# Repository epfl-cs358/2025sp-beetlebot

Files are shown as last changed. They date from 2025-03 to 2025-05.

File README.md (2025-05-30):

<h1 align="center">CS-358 Project: BeetleBot 🪲</h1>

---

**Contributors:** Anna Barberis, Omayma Hadiji, Adèle Monjauze, Jonas Zimmermann, Anas El Madhi

BeetleBot Animation

## Project Description

BeetleBot is a six-legged robot with 3 degrees of freedom on each leg. The idea is to mimic the walking pattern of an insect, or more specifically to implement a tripod-like motion. Walking on flat ground, a hexapod can implement many different gaits to move itself. The most popular ones include tripod gait, going forward, backward, and rotating, an crab walk-like motion. 
Thus, a hexapod demonstrates flexibility in how it can move and balance its weight. Our robot moves itself based on an input given by a user through a web application. 
It interacts with its surrounding with three sensors posted on the front and the side. Read more on the [project proposal]().

## Table of Contents
- [Hardware & Design Specifications](#hardware-and-design-specifications)
- [Software Specifications](#software-specifications)
- [Challenges](#challenges)
- [Installation Requirements](#installation-requirements)
- [Make your own BeetleBot](#make-your-own-beetleBot)
- [Pinouts](#pinouts)
- [Usage Instructions](#usage-instructions)
- [Troubleshooting](#troubleshooting)
- [Acknowledgments](#acknowledgments)

## Hardware And Design Specifications

[View 3D Model](documentation/full_bot.stl)

The goal of our 3D design was to keep it lightweight, as compact as possible, and avoid any unnecessary plastic. This led to minimalistic legs with sturdy joints, using just enough material to hold the servos tightly, all while eliminating unwanted movement and making sure the servos weren’t supporting their own weight. The legs were also made in such a way that they could fold on themselves and go the most downwards possible. Indeed, the more the legs aligned under the body, the less force the servos would require to hold the whole hexapod. Standing up with your legs far apart is much harder than standing up with your legs close together. Being able to fold on themselves is a very important aspect that was needed when the hexapod was standing up: for example, if you come out of a swimming pool with your arms far from your body, you will have a hard time getting up, while if theyre are close to it, it will be much easier.

The base was designed to support the heaviest items on the bottom for better stability, while the lid holds the materials that require the most convenient access. This resulted in having 6 servos and the battery, along with its protection board and the buck converter, on the bottom as they hold the most weight. The ESP32 and the servo multiplexer were placed on top as we often needed to change the ESP's or the multiplexer's cabling. The 6 servos that served as coxas were placed downwards and on the base so they wouldnt require any unecessary additional structure by being directly screwed on the floor of the base.
Finally, the base was designed with many holes to lighten it.

The final weight of the hexapod is 495g with an approximate size of 11 * 8.5 * 8 cm³ without the legs and 11 * 35 * 15 cm³ with the legs spread apart for the width of 35 cm and with the legs at their lowest for the height of 15cm.

## Software Specifications
The robot is capable of rotational, directional movements as well as standing / sitting (pose transitions). The implementation of those gait patterns works alongside real-time feedback from 3 VL53L1X sensors. The robot is controlled remotely through a webserial, or through input on a terminal (serial monitor) when plugged-in. 
The webpage accepts directional commands (North, East...) with additional curve orientations (North east, North West). The user can choose to toggle, on the webpage, between translational or rotational movement, and can also choose to toggle on sensor detection. If the sensor detection is on, the cycle of movement will stop if an object is in front, or on the sides, at a given distance. 
Here is a video to show of the [sensors](images/IMG_0313.MOV).
Each of our gaits are pre-defined. Real-time interpolation of those pre-defined angles is computed so that each leg moves smoothly, ie a leg contains three servos, and synchronizes with the whole 18 servos. 

The webpage and all of its content is loaded on the flash memory with SPIFFS, which makes it last between resets and not sent when uploading code. The website is processed in main.cpp, which changes the IP address of the websocket defined in it. This websocket is used to send updates between the control panel and the ESP. This is how the ESP get the last input and how the web page get the sensors' distances (used to update animations). The website takes input with a keyboard or with the joystick shown on screen. Both methods send the exact same data to the ESP, to simplify how it is handled.
Here is a video to show off [everything](images/video_2025-05-30_16-48-52.mp4)
## Challenges

- Hardware:
    - The challenges for the CAD was mainly the leg: We initially had a first design where the leg was unecessary long and heavy, with an added effect of the servos having to handle their own weight along with the rest of the leg. We did not realise immediately the importance of the design, thinking the servos would be able to hold it in any case. In fact, even with our now optimised design, they still struggle carrying the whole weight. The leg being too long was also problematic because this made it impossible for the hexapod to stand up or walk without putting too much force on the servos. It took some time but we finally managed to create a minimalistric design where the servos were tightly screwed to their joint. In consequence, the legs were much lighter and the servos did not have to hold their own weight anymore.
    - Another hardware challenge was the cable management. Indeed, we were facing a trio of cables for each servos, along with cables for the multiplexer, the battery, the sensors and the ESP32, totalling with a strong ~50 cables. We managed to make some of them fit inside the base, but the biggest problems was the cables that had to stay outside of the base since the multiplexer was on the lid. We ended up tying the servo cables together so they would not be everywhere around our hexapod.  
- Software:
    - One of the main challenges was trying to implement inverse kinematics (IK). While the math behind it was well-understood on paper, translating it to code was a bit more compilcated. The IK computations relied heavily on real-world measurements, such as the exact lengths of the leg segments and the position of the servos, and small differences made the leg movement inaccurate or unexpected. Tuning those parameters was particularly difficult, and we were short on time to completely dive in and properly understand what was wrong and how to fix it. We made compromises by gradually introducing motion interpolation and hardcoding the gaits we wanted, as explained on the last section.
    - Another challenge we faced was implementing an interface to control the bot over WiFi. This has been done with multiple libraries that are listed in our platformio.ini. The most notable are the webserver and the websocket: The first just sends a file when a GET request arrive, while the second is set between the webapp and the ESP to exchange information during execution. The webapp sends the input the bot must follow, while the ESP sends the distances recorded by sensors. This task didn't create as much trouble for us as other ones, but it required a lot of background knowledge for the different APIs and how everything needed to be connected.

## Installation Requirements

- Hardware requirements (e.g., components needed).
    - Electronics:
        - 18 servos (in our case it was servo SG90 but we would heavily recommand stronger ones)
        - 3 sensors(TOF400C) to place in front and on the sides
        - PCA 9685 PWM multiplexer to plug the servos (would advise to have two multiplexers instead of just one)
        - Esp32 Devkit V1 Board as a micro controller, or any esp32 that has WiFi
        - LiPo Battery 25C 1000mAh 2S
        - Protection Board for the battery (2 cell BMS)
        - Jst connectors to connect the protection board and the battery
        - LM2596 Buck Converter
        - Cables and tape for the cable management (very important)
    - CAD components:
        - a base to hold the battery, 6 servos that will serve as the Coxas of the legs.
        - a lid to screw on top of the base, where we can place the multiplexer, the ESP32 and the buck converter.
        - 3 sensor holders to place in between the base and the lid
        - 6 legs composed of 3 pieces each:
            - a first joint to link the Coxa and the Femur
            - a second joint to link the Femur and the Tibia
            - a toe with a TCP tip
- Software requirements: Open the code folder inside VSCode, and install the PlatformIo Extension.
    - Platformio will automatically update itself with the library in platformio.ini, so the one we already wrote can be used directly.
    - To use the robot:
        - Go to the platformIO tab on VSCode, then go to your board > "Build Filesystem Image". After this is finished, use "Upload Filesystem Image". This will send the data folder, containing the website, to the ESP's flash memory.
        - Upload the code to the ESP.

## Make your own BeetleBot:
- Print all the 3D parts inside this [folder](CAD)
- Soldering :
    - solder the protection board : 2-jst female connector to the 8.4V for the (+) and 0V for the (-) : This will be where you plug your battery.
    - Solder the protection board 2 : thick cables on 12.6V for the (+) and 4.2V for the (-) : This will be for the consumer side.
    - Solder the thick cables to the buck converter
    - Solder some cables (preferably thick) from the out pins of the buck converter and connect it to the general (+) and (-) circuit of your system.
It should look like this :
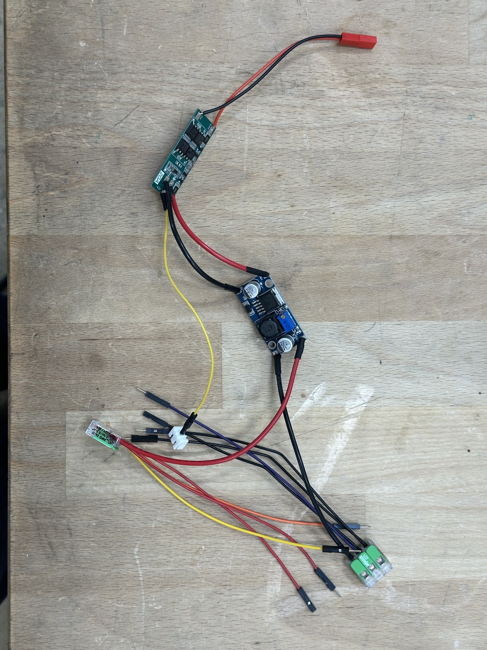
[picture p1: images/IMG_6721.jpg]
Soldering

- Screw on the 18 servos to the main body and on their joints: make sure to set them to a given angle (setAngle) inside data.h and put them on at a right angle to their joints
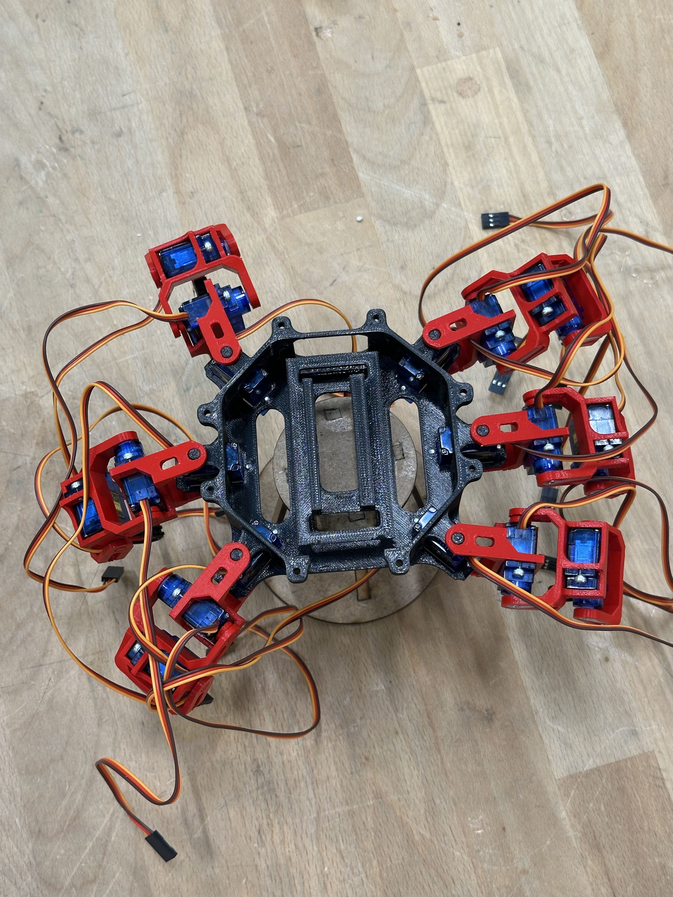
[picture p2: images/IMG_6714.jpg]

- Place the buck converter, the battery, the protection board, and the bundle of cables inside the body and screw on the lid on top
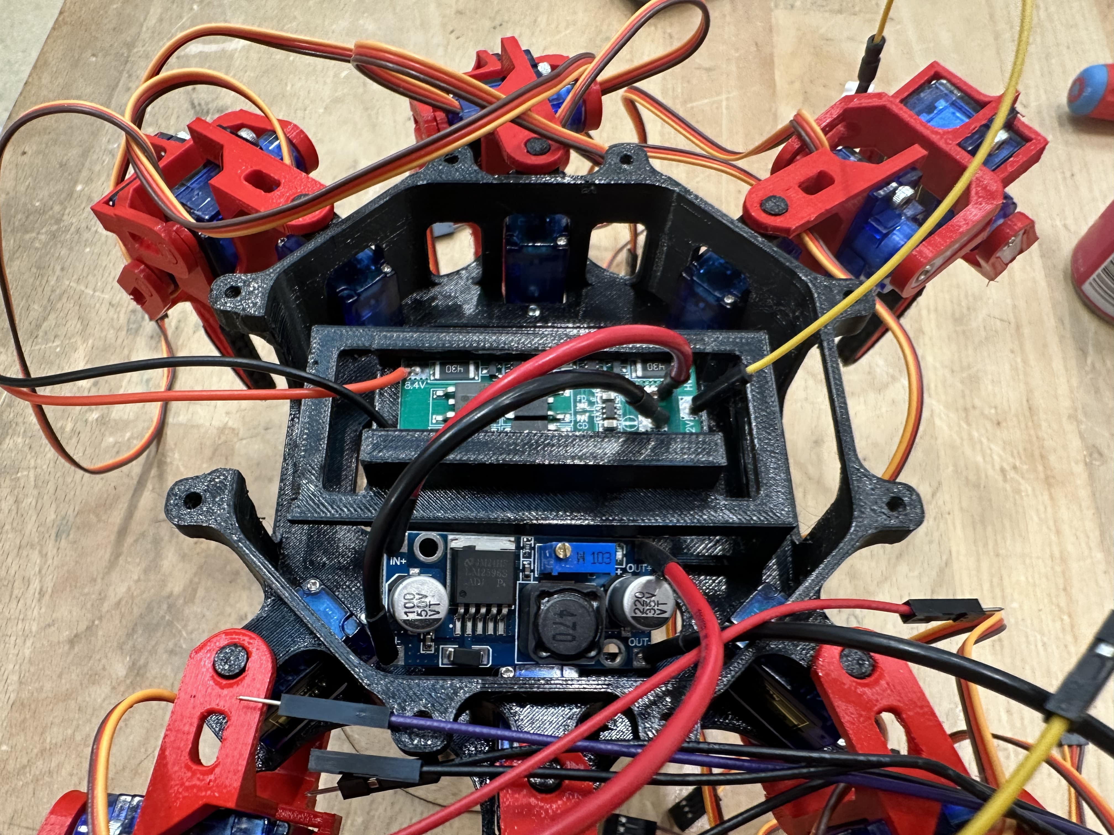
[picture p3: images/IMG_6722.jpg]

- Screw the multiplexer on the lid.
- Place the ESP32 in its sloth and crew the T stick figure on top to keep it in place.
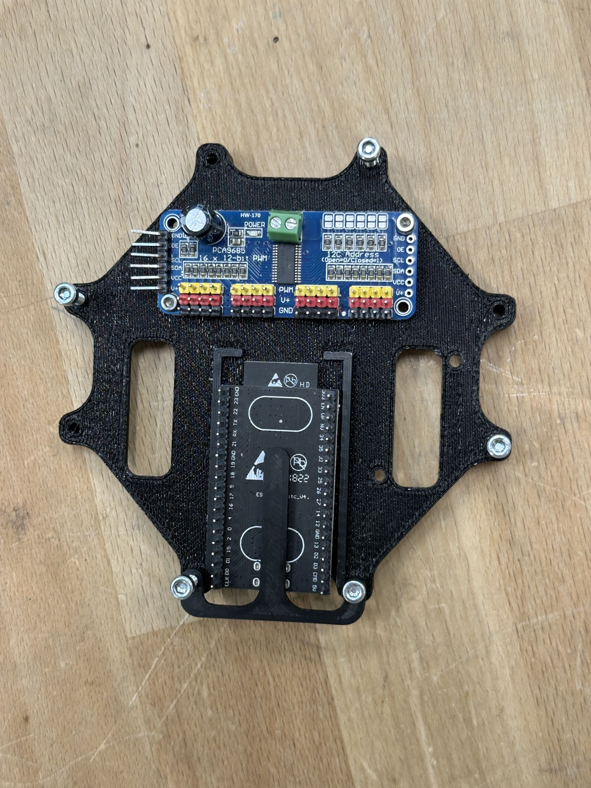
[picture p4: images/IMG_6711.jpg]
Lid

- Plug in all the servos on the multiplexer according to the mapping in the data.h, two of those servos (in our case the tibias of the two front legs) should be plugged in to the esp and powered from the power supply.
- Plug all the cables coming out of the multiplexer (SDA, SCL,...)
- Plug in the sensors on the esp, and screw them (or tape them).
- Finally, you can place a little hat on top and you're good to go!

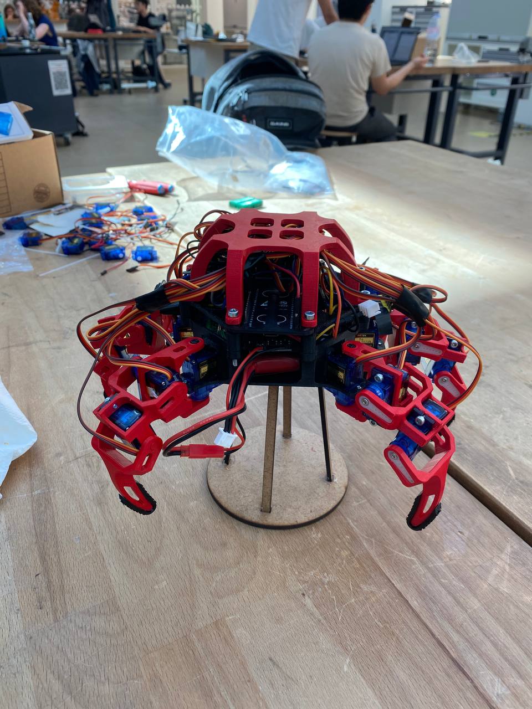
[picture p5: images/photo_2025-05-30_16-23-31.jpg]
Bot


## Pinouts
On Esp:
  - two servos PMW are plugged in on pin 18 and 23 of the ESP
  - SDA (pin 21) plugged to the multiplexer, and the sensors.
  - SCL (pin 22) plugged to the multiplexer, and the sensors.
  - 5V pin to power the esp
  - GND pin from the esp to the power supply

On the multiplexer:
  - Connect the power's (-) to the (-) of the multiplexer
  - Same for the (+)

For the sensors:
  - plug their SDA to the general SDA circuit
  - plug their SCL to the general SCL circuit
  - plug their (+) to the general (+) circuit
  - plug their (-) to the general (-) circuit

For the servos: plug them all on the multiplexer

Here is a picture of the circuit for additionnal help. Please note that for the cables that use the breadboard, this means you need to solder them together or clips them together :
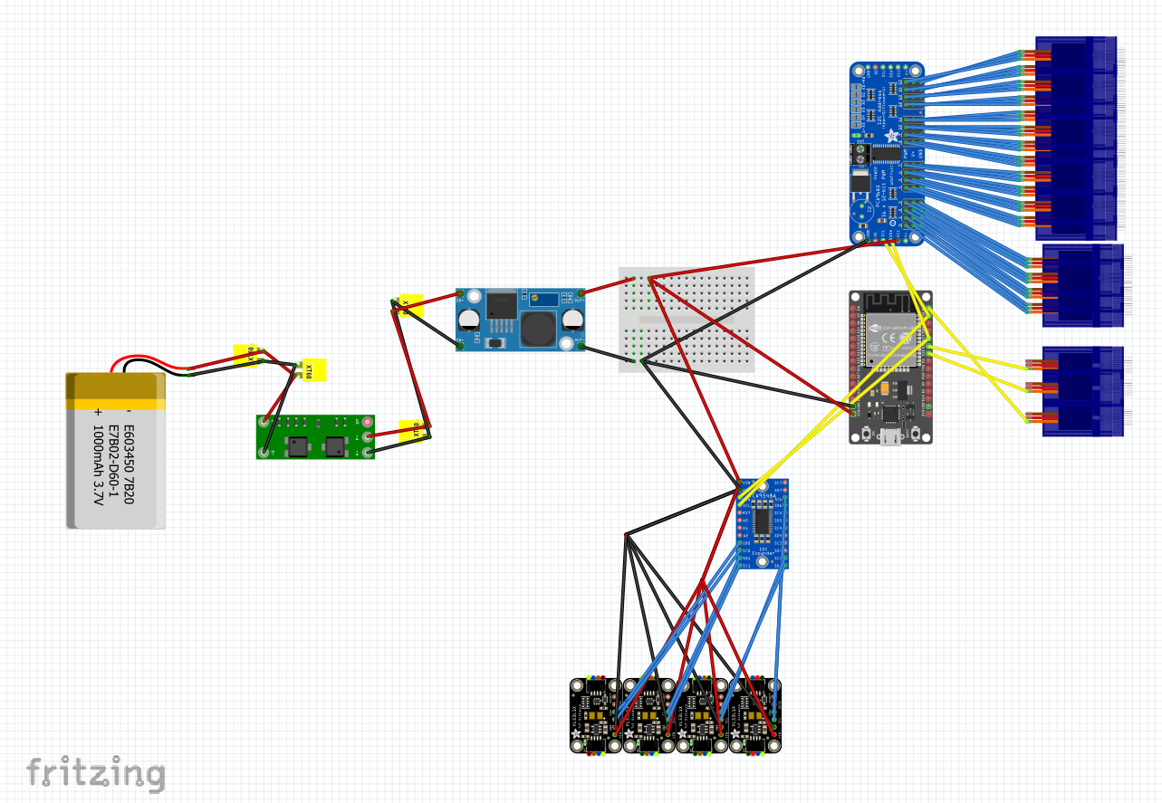
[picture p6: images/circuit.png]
Circuit Image

        
## Usage Instructions

Explain how to use your project. Include:
- Go on the wifi_credentials.h file
- Input the name of the wifi you will share with your ESP32 (You must both be on the same wifi)
- Put your wifi password
- Upload the code on the ESP32
- It will give you an IP adress: Copy paste it on your browser
- You will now be on the Web App: 
    - You can use the joystick to move around
    - You have different movement categories that you may change with the button 'change movement type'
    - Wether you are on AZERTY or QWERTZ, you can use THE WASD / ZQSD to move
- Have fun!
## Troubleshooting

There might be issues connecting to the ESP32 sometimes, it could be a port issue, if that is the case just look up and download 'CH340 driver'

## Acknowledgments

We'd like to thank all the servos and other components that had to die and/or suffer for this project to come to life! 

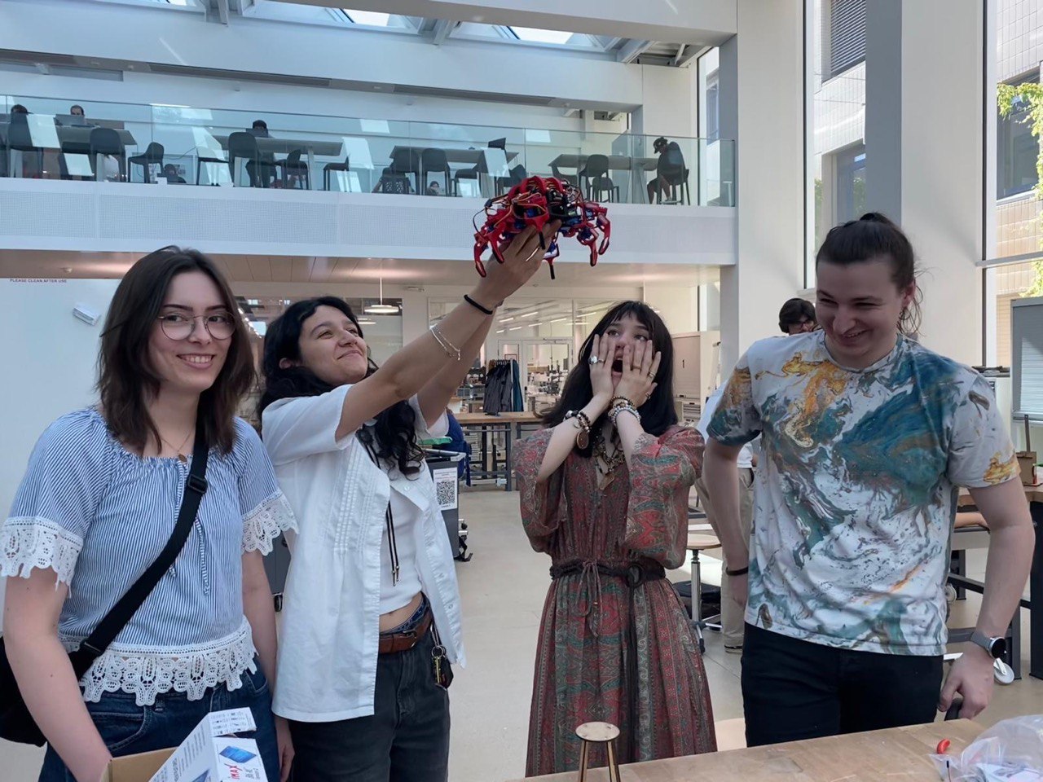
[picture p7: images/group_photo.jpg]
Group Photo


We thank all of our TAs and the teacher, especially Pinar Oray, Federico Stella and Mehdi Alaoui.

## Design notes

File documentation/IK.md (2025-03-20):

# Inverse Kinematics

## Introduction

Kinematics is the study of motion without considering the cause of such motion. such as forces and torques.
As opposed to forward kinematics, which computes the desired arrival coordinates of a robot given joint configuration as input, inverse kinematics (IK) is essentially the reverse operation, that is, computing joint configuration(s) to reach a desired arrival coordinate.
(**TLDR**: inverse kinematics is where you input where you want to go, and get the joint positions of how your robot needs to move in order to arrive at that position as output)

## Requirements

In order to compute the inverse kinematics of our BeetleBot, we will need the lengths of the joint sections, as well as some basic mechanical physics computations (into which we will input the joint lengths).

(The axis of the sketches are not indicative, they are only to visually show the different leg lengths)

<figure>
    <div style="display: flex; justify-content: space-between;">
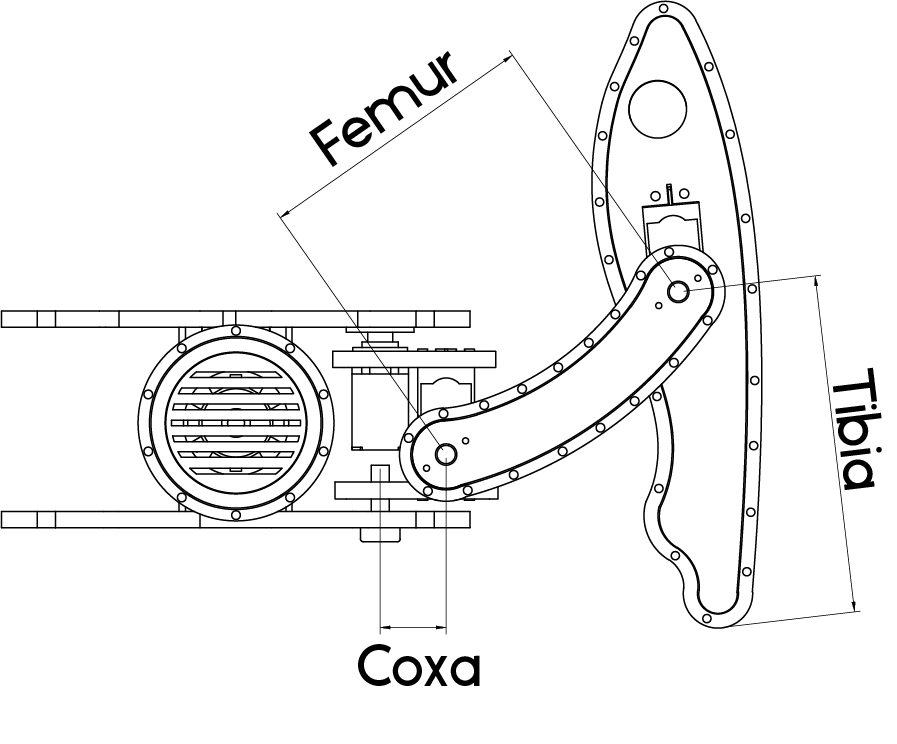
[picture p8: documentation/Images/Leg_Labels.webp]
Leg Labels
        
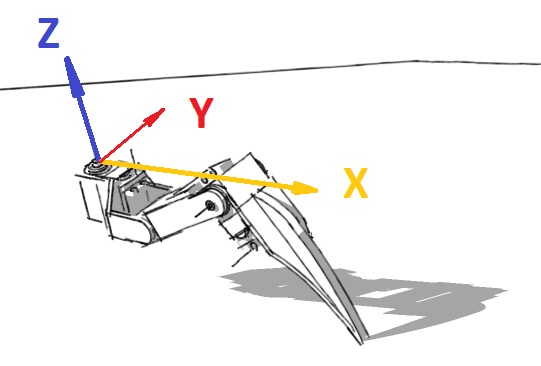
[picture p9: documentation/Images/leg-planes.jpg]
Leg Axis
        
    </div>
    <figcaption> Figure 1: Leg Labels (left) and Figure 2: Leg Axis (right) </figcaption>
</figure>

## Calculations

There are various online resources that have already done the brunt work of the mathematical and physics calculations that are needed in order to compute the inverse kinematics of walking robots. (I invite you to read up on the links in the sources for more precise details on the equations).
The [following](https://docs.google.com/spreadsheets/d/1CeIF2OFrUGDsMMskBs049kWXuV0JkgUp/edit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), (explanation [here](https://toglefritz.com/hexapod-inverse-kinematics-simulator/)) is a spreadsheet made to calculate all the required servo angles in order to have a basic translational walking gait. (Additional calculations will be needed in order to have different gaits, such as yaw, pitch, and roll, as illustrated via Figure 3.)

<figure>
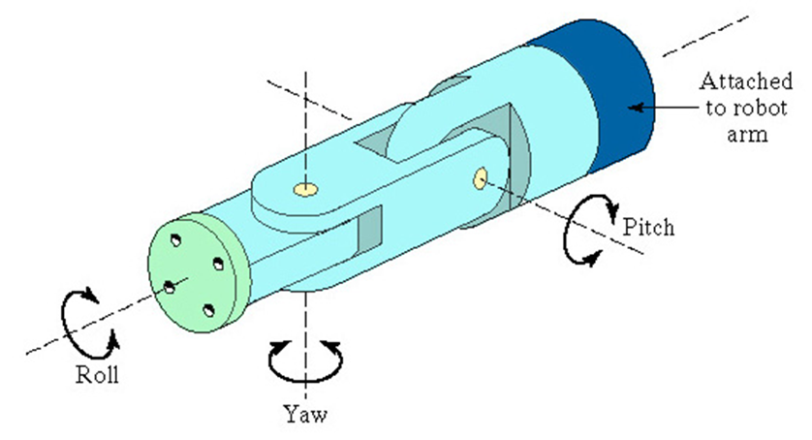
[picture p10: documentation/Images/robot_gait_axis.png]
Arm Axis
    
    <figcaption> Figure 3: Arm Gait Axis</figcaption>
</figure>

## Desired Movements

To achieve versatile and efficient movement, our hexapod robot should be capable of performing the following movements:
- Translational movement
  - Forward and Backward walking
  - Sideways walking (crab walk)
- Turning (Yaw)
- Pitch and Roll Adjustments

## Sources

- <https://toglefritz.com/hexapod-inverse-kinematics-equations/>
- <https://oscarliang.com/inverse-kinematics-and-trigonometry-basics/>
- <https://motion.cs.illinois.edu/RoboticSystems/InverseKinematics.html>

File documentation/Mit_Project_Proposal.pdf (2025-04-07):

# Proposal: BeetleBot

Anna Barberis, Omayma Hadiji, Jonas Zimmermann,

### Ad`ele Monjauze, Anas El Madhi

### March 2025

## 1 Description

The idea behind BeetleBot: BeetleBot, otherwise known as a Hexapod, is a six-legged robot with 3 degrees of freedom on each leg. The idea is to mimic the walking pattern of an insect, or more specifically to implement a tripod-like motion. Walking on flat ground, a hexapod can implement many different gaits to move itself. The most popular ones include tripod gait, reverse, and crab walk-like motion. The Beetlebot will also be able to interact and adapt to its surrounding, narrowing its stance to go through an obstacle-ridden path or avoiding objects ahead, to the sides, or behind itself. Thus, a hexapod demonstrates flexibility in how it can move and balance its weight. Our robot will respond to an input to direct itself, through a remote connection, like a game controller. It will also be able to make decisions based on its environment.

A deeper understanding: Stability is one of the keys to building a Hexapod. Using inverse kinematics equations, we will play with dynamic and static stability. Just like a human being can stand on one leg and shift his center of gravity, the same can be done for an hexapod (i.e. stand on half of its legs). If the center of mass of the robot is not probably balanced, the Hexapod will tip over.

### 1.1 Hardware

The selection of our electrical components was largely influenced by the choice of servos. To stay within our allocated budget while taking on the challenge of using relatively weak servos, we opted for SG90 servos to move the legs. They are lightweight, cheap, demand low power, and we have seen an existing project online that seemed to work using the full 18 of them. To connect the 18 + 1 servos together, we included a PCA 9685 PWM multiplexer. We also included 6 different servos, more powerful, but heavier and pricier. Those were included to be used on the weakest joint of the legs, the one that would bear the most weight, and that would be the most susceptible to break our SG90 servos. We plan to try with the weaker

1

servos first, and then decide later on if we want to replace them.

One of the main idea of this project was to have a connection between the robot and a remote controller directing the robot. This is why we decided to use a WIFI-Bluetooth compatible board. What oriented our choice to the ESP32-Devkit V1 board is its small size, as we want to avoid weighting down our robot as much as possible, and also that it had a large number of pins, which could be programmed to fit different protocols or interfaces like PWM (used by servos).

To enable the robot to interact with its surroundings and adapt its walking patterns based on environmental awareness, we selected 4 laser distance sensors. We chose laser sensors over alternatives due to their lightweight design, compact size, and suitability for our needs. Although integrating them may present some challenges in terms of coding, they are ideal for this application. To get a full view of the perimeter of the beetlebot, we will mount 2 sensors on one additional servo (the 19th one, an SG90), back to back. To cover any existing blind spots, we will add one sensor on each side of the mounted servo.
Since these sensors require an I2C interface, we needed an I2C multiplexer, that provided the sufficient number of pins with a unique address, to allow the microcontroller to differentiate them. The TCA9548A I2C multiplexer offers a unique I2C bus for each sensor.

To power our entire system, we chose a 7.4V 1000mAh 30C LiPo battery. This battery will supply power to the servos, microcontroller, and sensors through a DC buck converter that steps down the voltage to 5V. We aim for the robot to be self-sufficient with a single battery. As the servos each draw about 350mAh (stall) - 6.65A in total, the sensors about 40mAh - 160 mAh in total, and the microcontroller less than 100mAh, we estimated that one battery would be enough, given that all the servos won’t realistically move at the same time.
However, in the event that power consumption exceeds our expectations, or if we decide to upgrade to larger servos (which each draw 1.5A at 5V), we have opted to purchase two identical batteries for added capacity and reliability.
To connect the batteries to the system, we will use a 2S battery protection circuit, which will allow for a current draw of up to 10A, something that should be more than enough. We will also implement a switch, rated for the appropriate voltage and current, providing a means to safely power off the system when needed. More details on each components can be found in this section.
Omitting cables, screws and whatnot, the overall weight of all of our components should range up to 365g.

### 1.2 Software

We intend on implementing different gait patterns (crab-walk, reverse, tripod, forward...), which will involve mainly mathematical computation, to decide on angles, and positioning of the servos. The core of the software will focus on coordinating the movements of all the

2

servos, deciding which one should move and how the rest should adjust to counterbalance the motion. This will be a critical aspect of the project’s software development.

The next step software-wise to our project will be to code the laser distance sensors, and effectively let the objects around the robot change its way of moving. One of our key features will be enabling the robot to adopt a narrower stance to navigate between two obstacles, two walls. It will also be as simple as avoiding an object to any side of the robot, and pick a different path. This phase of the project will introduce more complexity and provide a more dynamic and interactive challenge for the robot’s navigation system.
In addition, we plan to integrate a remote-controller as an input method to control the robot’s directioning. The communication will go through the microcontroller, using WIFI or bluetooth. As an illustration, the idea would be that pressing one direction on the controller (a simple one composed of four arrows) would active certain servos and make the robot move in that requested direction. This software side could add user interaction to our beetlebot.

### 1.2.1 Inverse Kinematics (IK)

Inverse kinematics (IK) is the process of determining the joint (servo) positions required to reach a specific coordinate in space.
With our completed CAD design, we can accurately measure the lengths of each segment of the BeetleBot’s legs, which is crucial for performing IK calculations. These calculations allow us to determine how each servo should move to achieve precise leg positioning.
For a more detailed explanation, refer to the IK documentation in our GitHub repository. In brief, implementing IK enables us to program different gaits (walking modes) and is fundamental to achieving smooth and controlled movement of the hexapod.
For a deeper dive into IK equations for hexapods, the following (https://oscarliang.com/inverse-kinematics-and-trigonometry-basics/) resource provides a comprehensive overview.

### 1.3 Structure

The skeleton of our BeetleBot will primarily be constructed through 3D printing. Given the need for intricate and flexible, robust parts, this approach is ideal for creating the best possible structure of the bot. The design features a central base that will house all the electrical components, serving as the ”main body” of the bot. We want this center base to be as light, compact, and sturdy as possible. Its center of mass should be centered around the geometrical center of our beetle bot, to avoid tipping and ensure stability during movement.

The six legs will also be 3D printed. Each will consist of three main parts, most of which will be designed around the servos that drive them. By separating the legs into modular components, we can incorporate mobility at every joint where the parts connect, allowing for efficient movement through servo-actuated joints.
The first joint, located at the connection point with the central base, will act as the hip joint, enabling forward and backward movement of the leg. The second joint, located at the knee,

3

will allow up and down motion (knee folding movement). The third joint, located at the foot, will enable forward and backward movement, complementing the knee movement.
The leg dimension needs to be fine tuned to improve the weight distribution, and overall liberty of motion of the bot.
To improve the grip-ability of the legs, and avoid the robot from slipping, we may use rubber on the tips of the leg.
To protect our servos while trying out different designs and structure, we will consider adding ball casters extended by a printed piece so that they can support the center base. The idea is to use them strictly as ’training legs’.

## 2 Technical drawings

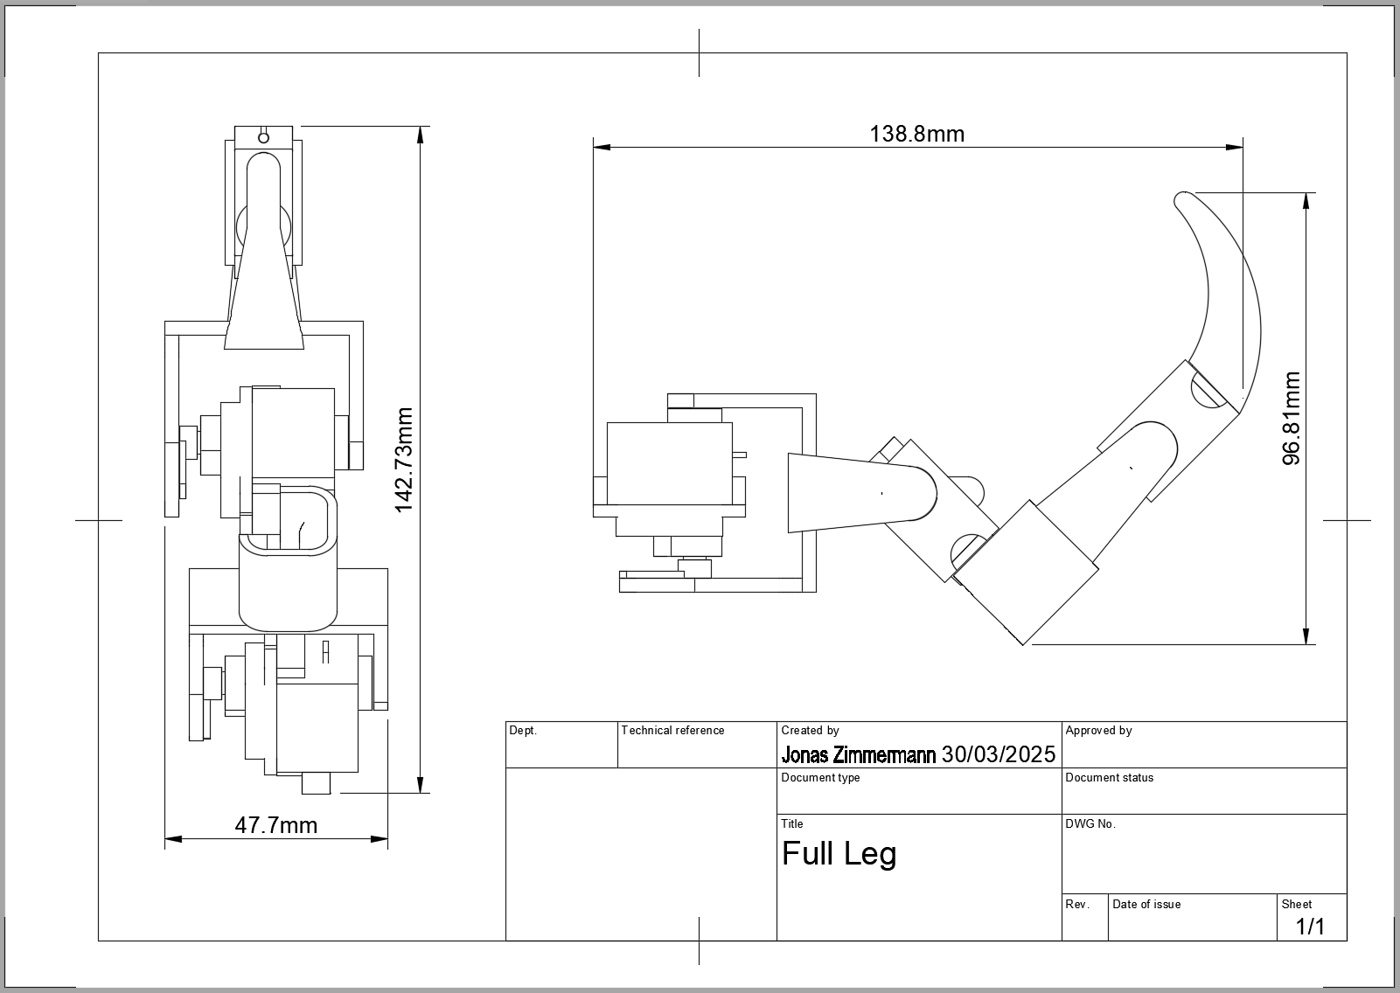
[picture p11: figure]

Figure 1: Drawing of a leg made with Fusion360

4

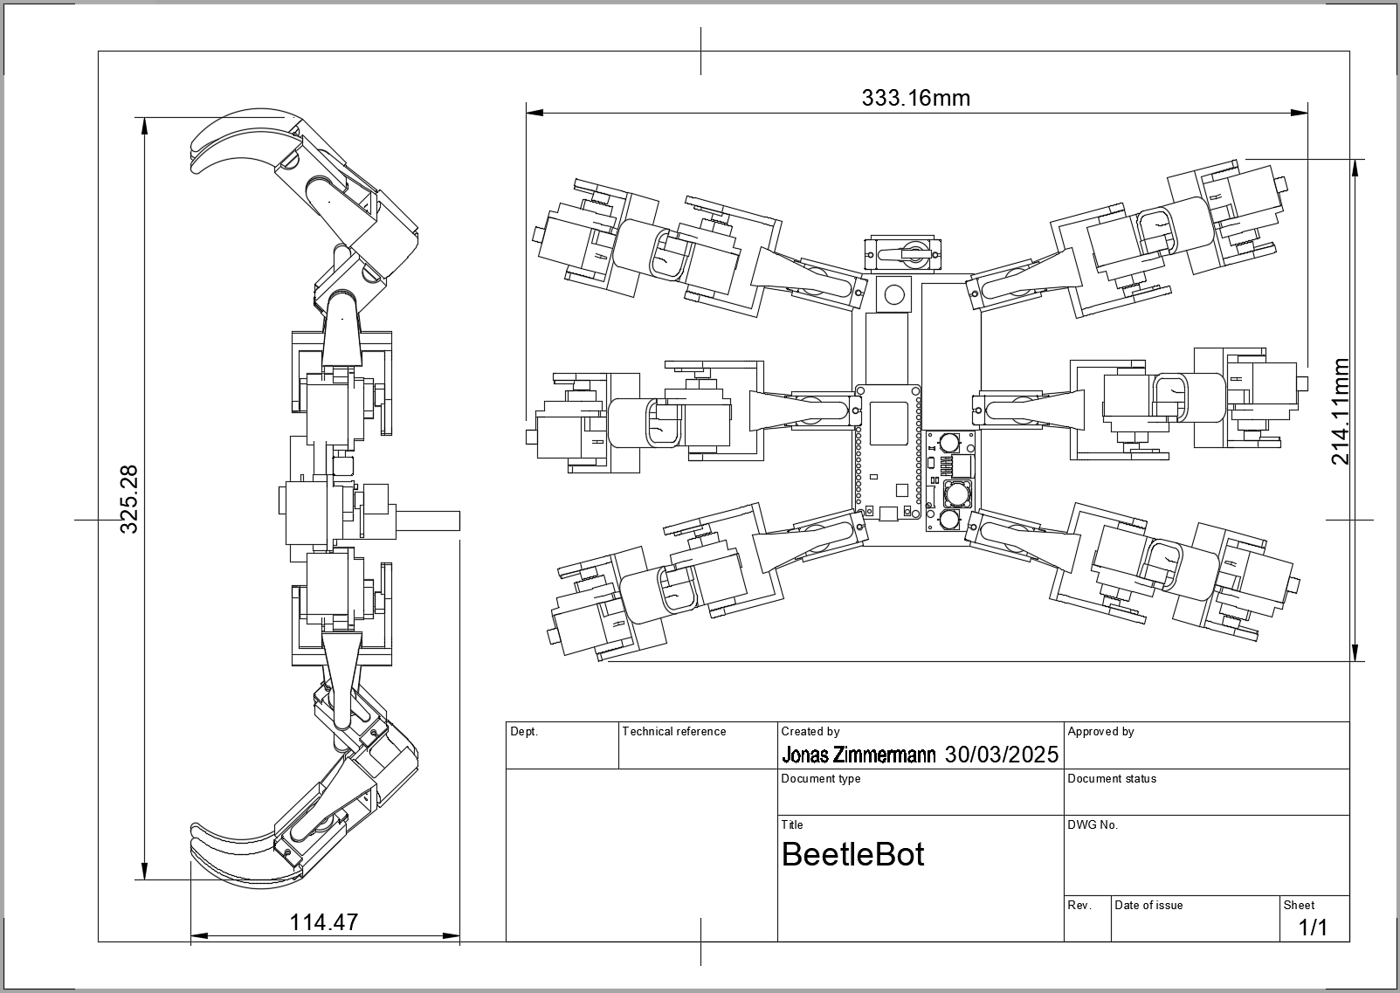
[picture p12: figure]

Figure 2: Drawing of the full bot

5

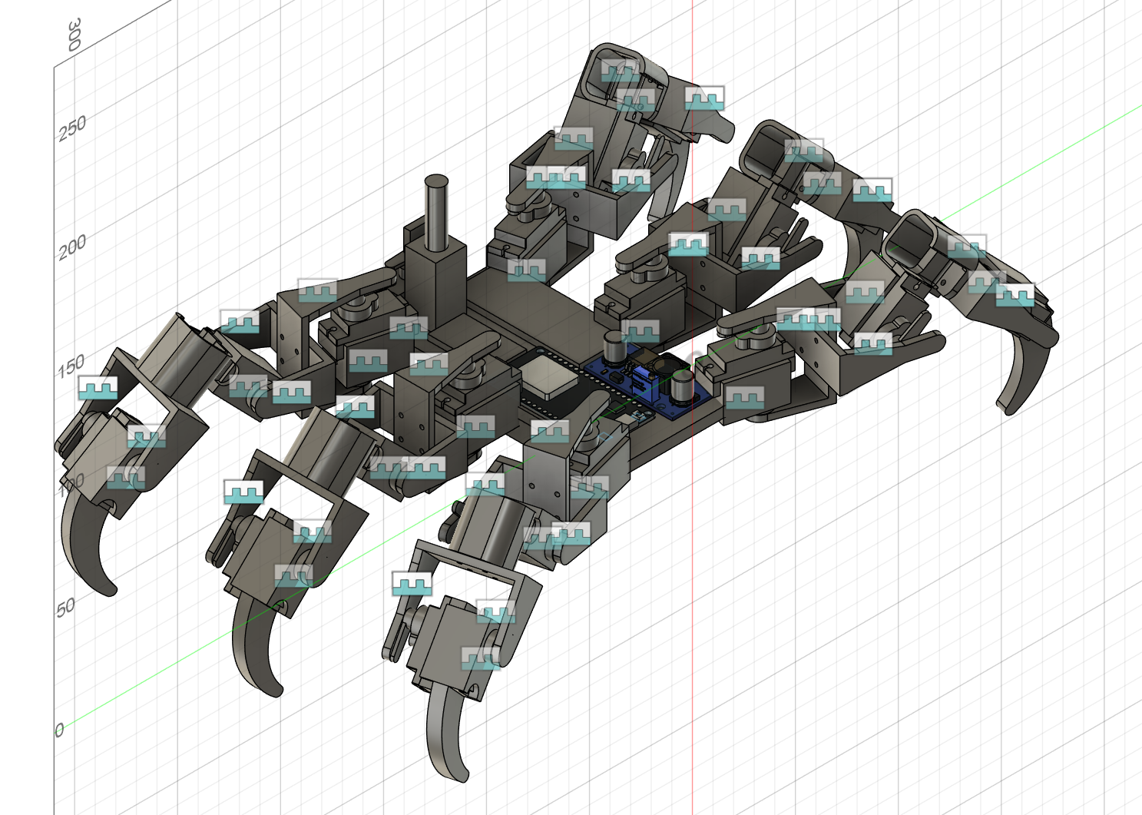
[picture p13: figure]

Figure 3: Screenshot of the bot made in Fusion360

6

### 2.1 Circuit diagram

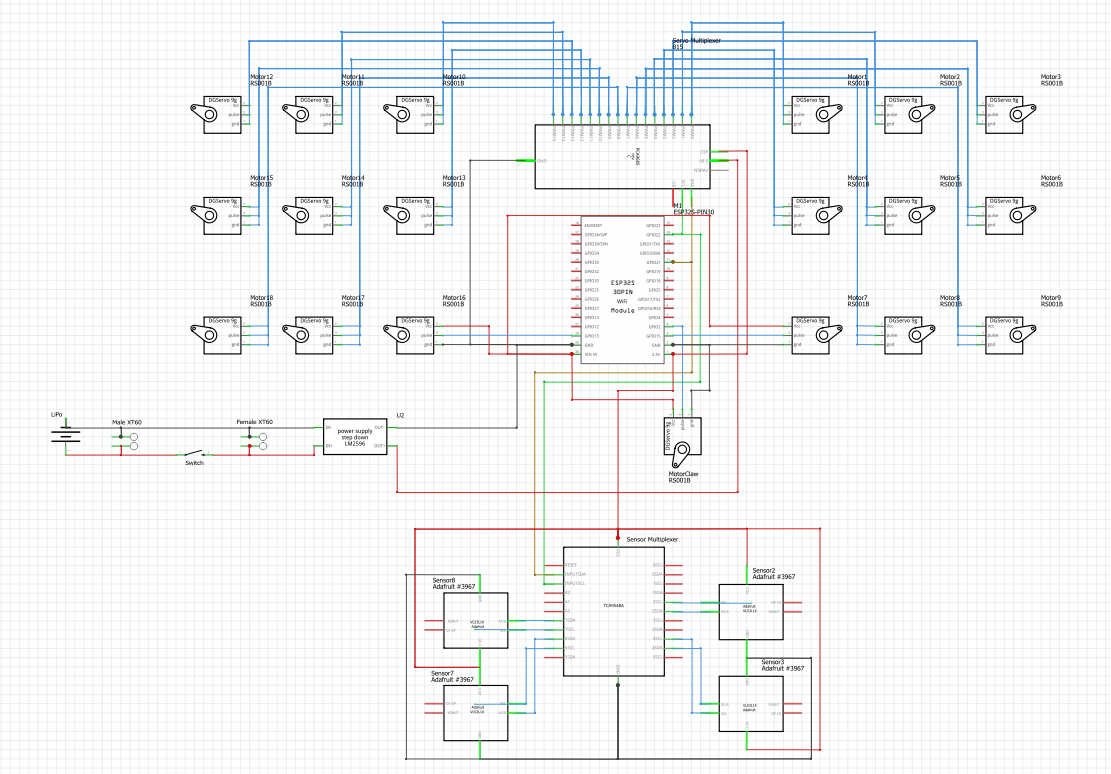
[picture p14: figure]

Figure 4: BeetleBot circuit diagram

7

## 3 Bill of Materials (BoM)

Category | Description | Quantity | Price
Power | LiPo battery 1000mAh 7.4V 30C XT60 (https://www.conrad.ch/fr/p/gens-ace-pack-de-batterie-lipo-7-4-v-1000-mah-nombre-de-cellules-2-30-c-bloc-xt60-3304661.html) | 2 | 17.5
Power | XT60 male connector (https://www.conrad.ch/fr/p/reely-re-6586515-fiche-male-pour-batterie-xt60-3-5-mm-a-souder-1-pc-s-2195505.html) | 2 | 2.1
Power | XT60 female connector (https://www.conrad.ch/fr/p/reely-re-6702318-prise-femelle-pour-batterie-xt60-dore-e-1-pc-s-2234106.html) | 2 | 2.7
Power | Charging cable XT60 (https://www.swaytronic.ch/en/SWAYTRONIC-charging-cable-XT60) | 1 | 5.6
Power | LiPo protection board for 2S | 2 | < 10
Power | LM2596 Buck Converter (https://www.conrad.ch/de/p/tru-components-spannungsregler-tc-9927140-1-st-2481785.html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) | 1 | 6.5
Power | On/Off Switch (https://www.distrelec.ch/en/toggle-switch-on-on-10-15-1co-apem-636h/p/13523834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) | 1 | 6.61
Wifi/ Bluetooth connection | Esp32 Devkit V1 Board (https://www.mouser.ch/ProductDetail/Espressif-Systems/ESP32-S2-DevKitC-1-N8R2?qs=vvQtp7zwQdN%252BQCxJ8G2wiQ==) | 1 | 7.07
Moving | SG90 servo motor | 19 | 57
Moving | MG996R servo motor (https://www.mouser.ch/ProductDetail/Terasic-Technologies/FXX-3037-TOP?qs=oIMkNKxjiKXvB5uXdyEV2A==) | 6 | 68.94
Moving | TOF400C laser sensor | 4 | 20
Sensors | TCA9548A I2C multiplexer (https://www.mouser.ch/ProductDetail/Adafruit/2717?qs=FXKxjuMTmBk%252BXQsxVhda7A==) | 1 | 6.14
Servos | PCA 9685 PWM multiplexer | 1 | 12
Miscellaneous (as training legs) | Ball casters (https://www.berrybase.ch/pololu-ball-caster-0-5-zoll-metallkugel-abs-gehaeuse-hoehenverstellbar-fuer-kleine-roboter) | 4 | 9
| | TOTAL | 231.16

Note: for the protection boards, our current consumption should not exceed 10A

## 4 Risk Assessment

### 4.1 Weight and Servo Strength

One of the main challenges we foresee is related to the weight of the hexapod and the strength of the servos. We are using relatively weak servos, so it is crucial that our design remains as light as possible. Achieving this will be challenging, as reducing weight often comes at the cost of structural integrity or functionality.
To mitigate this risk, we have brainstormed potential solutions in case the servos are unable to support the hexapod’s weight:
- Incorporating ball casters under the base: This would allow the hexapod to roll on small metal balls rather than relying entirely on the servos to lift and move its body.
- Optimizing material choice and frame design: Using lightweight yet sturdy materials such as carbon fiber, aluminum, or 3D-printed lightweight plastic could significantly reduce weight without compromising strength.
- Reevaluating servo selection: If initial tests indicate that the servos struggle too much, we will need to consider stronger alternatives, though this would impact power consumption.

8

Before implementing any of these solutions, we plan to prototype the hexapod with the lightest and most efficient design possible. This will allow us to assess whether the additional support mechanisms, such as ball casters, are necessary.

### 4.2 Servo Movements and Walking Mechanics

While we have a general idea of the gait patterns our hexapod will use (e.g., tripod gait), we have yet to determine the exact servo angles required for each step. This is not a trivial issue, as each leg will be controlled by at least two servos (one at the hip and one at the knee), and their precise coordination is essential for stable movement.
Key challenges include:
- Angle calculation and optimization:
- Each servo must move within its range while maintaining balance and fluidity in motion.
- The stationary legs (those on the ground) will still need to move at the hip to follow the body’s displacement.
- Adjusting these angles manually could be a tedious process, requiring a mix of trial-and-error testing and kinematic calculations.
- Inverse kinematics (IK) and load distribution:
- While we have done some preliminary research on inverse kinematics, and there is lengthy documentation available online about how the equations were determined for certain Hexapod designs, we still lack a deep understanding of how to minimize the force applied to the servos during movement.
- The lever arm effect (longer leg segments increasing torque requirements) must be taken into account.
- We can reference existing hexapod designs available online to refine our approach. (See Section 8 for such examples)

As mentioned earlier, if we cannot find an optimal leg design, we may still implement rolling support under the base to reduce strain on the servos.

### 4.3 LiPo Battery Use

Using a LiPo battery to power the entire system (servos, ESP32, sensors) adds complexity in terms of voltage regulation and current delivery. If the battery cannot supply enough current during peak loads (when multiple servos move simultaneously), it may cause voltage drops, system instability, or even resets.

Why it’s a challenge:

9

- We’re powering many components from one battery.
- Servos can pull a lot of current when moving together.
- If the voltage isn’t stable, the microcontroller might crash or the servos might glitch.

How we’ll deal with it:

- Use a LM2596 buck converter to get a steady 5V out of the LiPo.
- Test how much current the servos actually draw under load.
- Monitor the battery voltage so we know when it’s getting low.
- Use the second battery to split the usage

### 4.4 Software Challenges

### 4.4.1 Control of the servos

Controlling 18 servos in software, especially in coordination, brings several challenges related to timing, synchronization, and responsiveness. We’ll need to ensure that the walking behavior is smooth and that servo commands don’t conflict or overload the control bus.
We can:
- Use non-blocking code and timers to ensure responsiveness.
- Start with basic movement primitives (e.g. lift leg, move forward) and build up to full gaits.
- Simulate and visualize movements if possible before testing on hardware.

### 4.4.2 Remote Controller

If we implement remote control (e.g. over Bluetooth or Wi-Fi), we introduce another layer of software complexity. Parsing incoming commands, dealing with connection issues, and integrating this with walking logic needs to be done carefully. Indeed, handling both remote control input and real-time walking requires multitasking, and there is a risk of tight coupling between communication and motion logic, which would make debugging harder.
For this issue we therefore can:
- Keep communication logic modular and separate from walking control
- Define a clear and minimal communication protocol (e.g. fixed-length messages or JSON)

10

## 5 Organisation

### 5.1 Milestones

To organize our work, we will divide the task into three main milestones.

First off, we will focus on building a simple version of our bot, carefully designing the 3D parts, as every design choice will impact the successful-ness of our robot. Given that the weight of the components and their placement will impact the stability of our BeetleBot. Once this is secured, we will implement a simple gait pattern to get familiar with the servos, such as the forward walk, without any added challenge. It will be mainly hardware focused, with an introduction to the software side at the very end of this milestone. This milestone is the most important one, as most of the challenges that this project arises will be tackled : weight management, physics, or simply communicating with dozens of servos (ie: see risk assessment).

The second milestone will improve our already existing robot, by adding sensors, and implementing more interesting gait patterns. Sensors will help us implement our robot’s interaction with its environnment. This milestone will allow us to dive in more into the software side of our BeetleBot, notably coding the sensors, together with the servos.

The third milestone will also involve a software side, to make our bot responds to a remote input thanks to our wifi/bluetooth connective microcontroller. As this milestone is the last one,is quite challenging, and our bot should be functional by then, we consider this milestone as optional.

### 5.2 Work breakdown

11

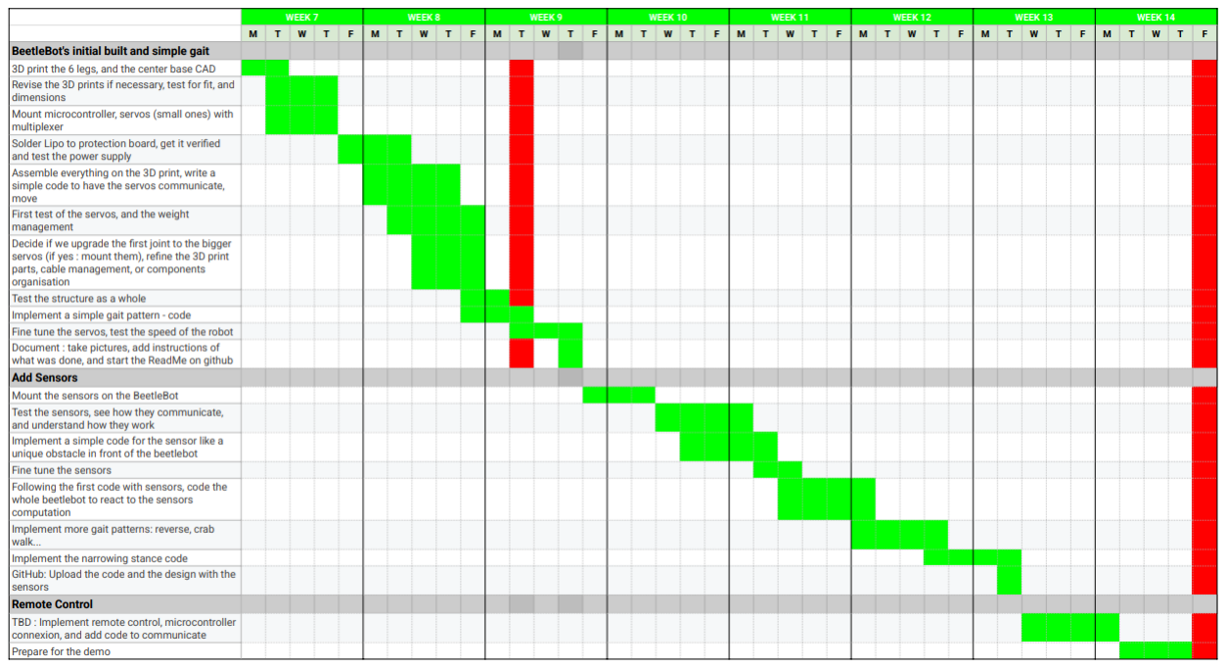
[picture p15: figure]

Figure 5: BeetleBot organisation chart

## 6 User stories

Biomechanics Researcher
As a biomechanics researcher, I want to analyze the hexapod’s gait efficiency and compare it to biological arthropods to test hypotheses about energy optimization in locomotion. I want to study how different gaits affect energy expenditure, stability and speed. I can use the hexapod to validate hypothesis about insect movement. A similar (https://www.youtube.com/watch?v=QZt3eJzHLSU) study has been conducted by EPFL researchers.

CS358 Teacher
As an instructor, I want the hexapod to serve as a modular platform for teaching robotics principles, enabling students to experiment with gait algorithms, sensor integration, and collaborative problem-solving. I can challenge my students to improve the gait efficiency or implement terrain adaptation using sensor feedback.

Robotics Engineer
As a robotics engineer, I want to prototype and test new gait algorithms to improve the hexapod’s adaptability to unstructured terrains. I can test the servo durability, torque and energy consumption under load to simulate real-world scenarios.

12

## 7 Future of the BeetleBot

The BeetleBot project can serve as a strong foundation for future research and development in the field of bio-robotics. By building upon its existing capabilities, we can expand its functionality, enhance its real-world applications, and push the boundaries of biologically inspired robotics. For example, the BeetleBot’s current laser distance sensors provide basic obstacle detection, but integrating computer vision could revolutionize its environmental awareness. By adding lightweight cameras (e.g., Raspberry Pi) and leveraging machine learning, the robot could:
- Identify and classify objects (e.g., differentiating between obstacles, tools, or targets).
- Adapt its gait dynamically based on terrain (e.g., stepping over gaps or adjusting stride on slippery surfaces).
- Perform SLAM (Simultaneous Localization and Mapping) for autonomous navigation in unknown environments.

Another improvement can be made in regards to the motion of the hexapod. The current gait system relies on pre-programmed inverse kinematics, but future iterations could use reinforcement learning (RL) to:

- Self-optimize movement efficiency by testing different gaits and learning which ones minimize energy consumption.
- Adapt to damage (e.g., if a leg is impaired, the AI could recalibrate its walking pattern).
- Simulate bio-inspired behaviors (e.g., cockroach-like scrambling over obstacles or antlike cooperative carrying).

Furthermore, the current BeetleBot design uses SG90 micro servos for most joints, prioritizing cost and weight savings. However, upgrading to higher-torque servos (e.g., MG996R or Dynamixel AX-12A) could unlock significant improvements in movement quality and durability. This would unlock many new capabilities and functionalities, such as stronger torque for smoother motion, longer lifespan, support for heavier payloads (such as ithe integration of additional sensors), but this would require a redesign of the current body, as it would need to accomodate the bigger servos and potentially a bigger battery.

## 8 References, inspiration

We have drawn some inspiration from existing Hexapods online, and tried to build our own project out of it. Some of those references include:
[1] Hexapod using SG90 motors (https://www.instructables.com/Simple-NodeMCU-18-DOF-Hexapod/)
[2] Complex Hexapod using MG996R motors (https://www.instructables.com/Capers-II-a-Hexapod-Robot/)
[3] Code computation references, inverse kinematics (https://arduin0.blogspot.com/2012/01/inverse-kinematics-ik-implementation.html)
[4] Inverse kinematics, leg design (https://toglefritz.com/hexapod-inverse-kinematics-equations/)

13

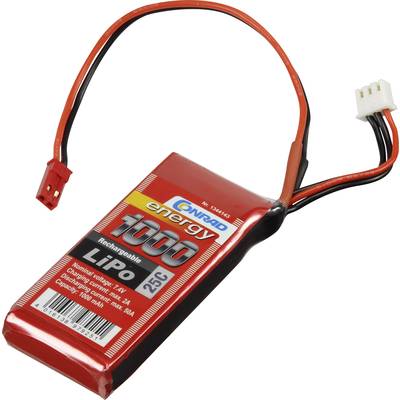
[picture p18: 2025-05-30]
images/LiPo.jpg

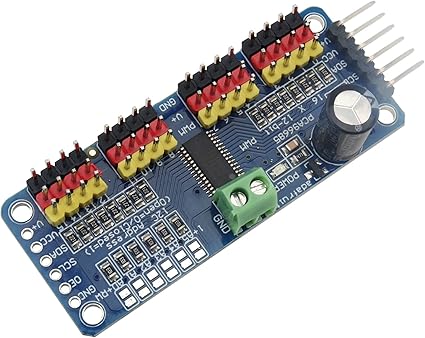
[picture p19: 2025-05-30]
images/PCA9685.jpg

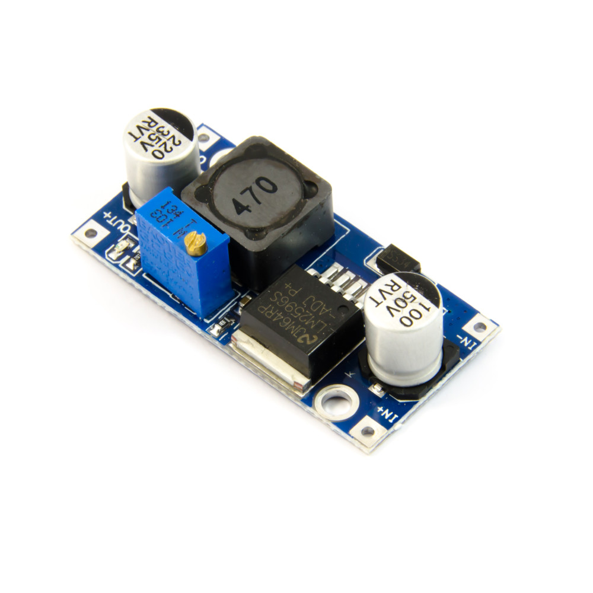
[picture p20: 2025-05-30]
images/buckConverter.jpg

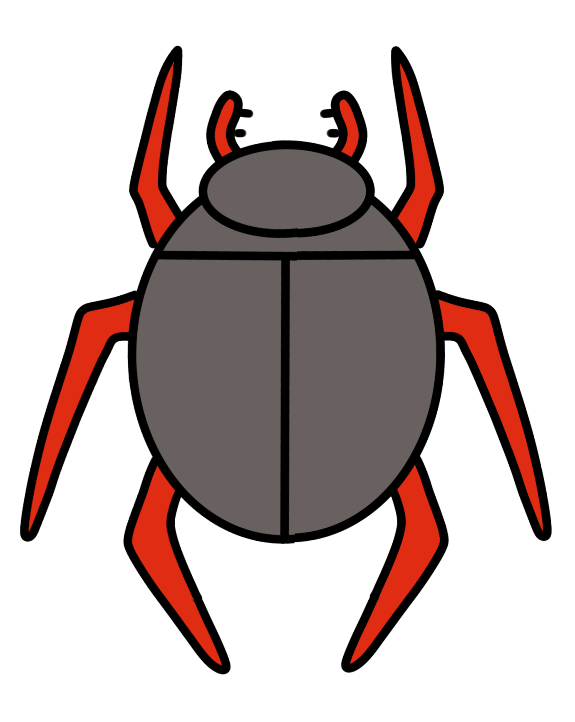
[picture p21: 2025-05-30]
images/beetle.PNG

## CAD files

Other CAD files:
CAD/Chaussette.f3d
CAD/Full Leg.f3z
CAD/Joint1.f3z
CAD/Joint2.f3z
CAD/Toe.f3d

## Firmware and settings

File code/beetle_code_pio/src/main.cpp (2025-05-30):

#include "main.h"
#include <Adafruit_PWMServoDriver.h>

Adafruit_PWMServoDriver multiplexer = Adafruit_PWMServoDriver(0x40);
AsyncWebServer server(80);
String wifistr;
char lastInput[3] = "C";
int lastDists[3] = {0};
bool satDown = false;
int distSensorMin = 0;
int distSensorMax = 150; 
bool movementType = true; // if sets to true, the robot rotates on itself to get to the direction
//false : goes in the direction without rotating, i.e. crabwalk / backwards
bool sensorDetect = false;

// create an easy-to-use handler
static AsyncWebSocketMessageHandler wsHandler;

// add it to the websocket server
static AsyncWebSocket ws("/ws", wsHandler.eventHandler());

leg lf = leg(multiplexer, lfCOffset, lfFOffset, lfTOffset, "lf", 0, 
    servoPins[0][Coxa], servoPins[0][Femur], servoPins[0][Tibia]);
leg rf = leg(multiplexer, rfCOffset, rfFOffset, rfTOffset, "rf", 1, 
    servoPins[1][Coxa], servoPins[1][Femur], servoPins[1][Tibia]); 
leg lm = leg(multiplexer, lmCOffset, lmFOffset, lmTOffset, "lm", 2, 
    servoPins[2][Coxa], servoPins[2][Femur], servoPins[2][Tibia]);
leg rm = leg(multiplexer, rmCOffset, rmFOffset, rmTOffset, "rm", 3, 
    servoPins[3][Coxa], servoPins[3][Femur], servoPins[3][Tibia]);
leg lb = leg(multiplexer, lbCOffset, lbFOffset, lbTOffset, "lb", 4, 
    servoPins[4][Coxa], servoPins[4][Femur], servoPins[4][Tibia]);
leg rb = leg(multiplexer, rbCOffset, rbFOffset, rbTOffset, "rb", 5, 
    servoPins[5][Coxa], servoPins[5][Femur], servoPins[5][Tibia]);     

//Default for manual control of joints
unsigned int offsetAngle = 5;

static bool multiplexerOk = true;
static unsigned long lastCheck = 0;

movements motion = movements(lf, rf, lm, rm, lb,rb, multiplexer, 15);
leg *current = motion.current;

String processor(const String& var){
  Serial.println(var);
  if(var == "ADDR"){
    return wifistr;
  }  
  return String();
}

void setup () {
    Serial.begin(9600);
    
    if (WEB_SERIAL) {
        //To check if the password and ssid are correct
        Serial.println(PROGMEM "Connecting to WiFi...");
        Serial.println(WIFI_SSID);
        
        WiFi.mode(WIFI_STA);
        WiFi.begin(WIFI_SSID, WIFI_PASS);
        
        if (WiFi.waitForConnectResult() != WL_CONNECTED) {
        Serial.printf(PROGMEM "WiFi Failed!\n");
        return;
        }
        
        // WebSerial is accessible at "<IP Address>/webserial" from your browser
        Serial.print(PROGMEM "IP Address: ");
        Serial.println(WiFi.localIP());
        wifistr = WiFi.localIP().toString();

        if(!SPIFFS.begin(true)){
            Serial.println(PROGMEM "An Error has occurred while mounting SPIFFS");
            return;
        }
        
        server.on("/", HTTP_GET, [](AsyncWebServerRequest *request) {
            request->send(SPIFFS, "/index.html", String(), false, processor);});

        server.on("/joy.js", HTTP_GET, [](AsyncWebServerRequest *request){
            request->send(SPIFFS, "/joy.js","text/javascript");});

        server.on("/style.css", HTTP_GET, [](AsyncWebServerRequest *request){
            request->send(SPIFFS, "/style.css","text/css");});

        server.on("/favicon.ico", HTTP_GET, [](AsyncWebServerRequest *request){
            request->send(SPIFFS, "/favicon.ico","image/x-icon");});

        server.on("/bot.png", HTTP_GET, [](AsyncWebServerRequest *request){
            request->send(SPIFFS, "/bot.png","image/png");});

        wsHandler.onMessage([](AsyncWebSocket *server, AsyncWebSocketClient *client, const uint8_t *data, size_t len) {
            if (strcmp((const char*) data, "MC") == 0) {
                movementType = !movementType;
            } else if (strcmp((const char*) data, "DE") == 0) {
                sensorDetect = !sensorDetect;
            } else memcpy(lastInput, data, 2);
        });


    server.addHandler(&ws);
    server.begin();
    }

    //Sensors code
    Wire.begin();
    Wire.setClock(400000); // use 400 kHz I2C
    forceSetup(); // after, the sensors should be all setup
    Serial.println("Sensors connected successfully! ");

    multiplexer.begin();
    multiplexer.setPWMFreq(60);

    ledcSetup(0, 50, 16);
    ledcSetup(1, 50, 16); 
    ledcAttachPin(servoPins[0][Tibia], 0); 
    ledcAttachPin(servoPins[1][Tibia], 1); 

    motion.initializeAllServos(standAngle[Coxa], standAngle[Femur], standAngle[Tibia]);
    printHelp();
}

bool isMultiplexerConnected(uint8_t address = 0x40) {
    Wire.beginTransmission(address);
    return (Wire.endTransmission() == 0);
}

void loop() {
    for(int i = 0; i < 3; ++i){
        int val = checkSensor(i);
        if (val > 0) {
            lastDists[i] = val;
        } else if (val == -1) {
            lastDists[i] = 0;
        }
    }

    ws.cleanupClients();
    sendJson();

    if (WEB_SERIAL) {
        switch (lastInput[0]){
            case 'N':
                if (satDown || (sensorDetect && lastDists[1]<=distSensorMax && lastDists[1]>distSensorMin)) break;
                if (lastInput[1] == '\0') {
                    motion.forward();
                } else if (lastInput[1] == 'E') {
                    motion.forwardCurve(1, 0.5);
                } else if (lastInput[1] == 'W') {
                    motion.forwardCurve(0, 0.5);
                }
                break;
            case 'S':
                if (satDown) break;
                if (lastInput[1] == '\0') {
                    if (movementType) {
                        motion.rotation(1, 7);
                    } else {
                        motion.backward();
                    }
                } else if (lastInput[1] == 'E') {
                    if (movementType) {
                        motion.rotation(1, 4);
                    } else {
                        motion.backwardCurve(1, 0.5);
                    }
                } else if (lastInput[1] == 'W') {
                    if (movementType) {
                        motion.rotation(0, 4);
                    } else {
                        motion.backwardCurve(0, 0.5);
                    }
                }
                break;
            case 'E':
                if (satDown || (sensorDetect && lastDists[0]<=distSensorMax && lastDists[0]>distSensorMin)) break;
                if (lastInput[1] == '\0') {
                    if (movementType) {
                        motion.rotation(1, 4);
                    } else {
                        motion.sideways(0);
                    }
                }
                break;
            case 'W':
                if (satDown || (sensorDetect && lastDists[2]<=distSensorMax && lastDists[2]>distSensorMin)) break;
                if (lastInput[1] == '\0') {
                    if (movementType) {
                        motion.rotation(0, 4);
                    } else {
                        motion.sideways(1);
                    }
                }
                break;
            case 'U': 
                if (satDown) {
                    motion.standUp();
                    satDown = !satDown;
                } else {
                    motion.sitDown();
                    satDown = !satDown;
                }
                break;
            case 'B': 
                if (satDown) break;
                motion.wave();
                break;
            default:
                sleep(1);
                break;
        }
    } else {
        handleSerialInput();
    }

    
}

void handleWifiSerialInput(const uint8_t *data, size_t len) {
    String input = String((const char*) data);
    input.trim();

    if (input.length() == 1) {
        handleKeyCommand(input.charAt(0));
    } else {
        handleTextCommand(input);
    }
}

// Depreciated serial input function, left for reference
void handleSerialInput() {
  if (Serial.available() > 0) {
    String input = Serial.readStringUntil('\n');
    input.trim();
    if (input.length() == 1) {
      handleKeyCommand(input.charAt(0));
    } else {
      handleTextCommand(input);
    }
  }
}


void handleTextCommand(String input) {
    input.toLowerCase();
    
    for(uint8_t i = 0; i < 6; i++) {
        if(input == motion.legs[i]->name) {
          current = motion.legs[i];
          Sprint(PROGMEM "Selected leg: ");
          Sprintln(current->name.c_str());
          return;
        }
    }
    
    if (input.startsWith(PROGMEM "offset ")) {
        String offsetValue = input.substring(7); // Extract the value after "offset "
        int newOffset = offsetValue.toInt(); // Convert to integer
        if (newOffset > 0) { // Ensure it's a valid positive number
            offsetAngle = newOffset;
            char temp[5] = {0};
            itoa(offsetAngle, temp, 10);
            Sprint(PROGMEM "Offset angle set to: ");
            Sprintln(temp);
        } else {
            Sprintln(PROGMEM "Invalid offset value. Please provide a positive number.");
        }
    } else if (input == "forward") {
        motion.forward();
    } else if (input == "backward") {
        motion.backward();
    } else if(input == "help") {
        printHelp();
    } else if(input == "stand") {
        motion.initializeAllServos(standAngle[Coxa], standAngle[Femur], standAngle[Tibia]);
    } else if(input == "sit") {
        motion.initializeAllServos(sitAngle[Coxa], sitAngle[Femur], sitAngle[Tibia]);
    } else if(input == "test set") {
        motion.initializeAllServos(setAngle[Coxa], setAngle[Femur], setAngle[Tibia]);
    } else if(input == "stand up") {
        motion.standUp();
    } else if (input == "sit down") {
        motion.sitDown();
    } else if(input == "rot cw") {
        motion.rotation(1, 5);
    } else if(input == "rot ccw") {
        motion.rotation(0, 5);
    } else if(input == "forw cw") {
        motion.forwardCurve(1, 0.7);
    } else if(input == "forw ccw") {
        motion.forwardCurve(0, 0.5);
    } else if(input == "back ccw") {
        motion.backwardCurve(0, 0.5);
    } else if(input == "back cw") {
        motion.backwardCurve(1, 0.5);
    } else if(input == "left") {
        motion.sideways(1);
    } else if(input == "right") {
        motion.sideways(0);
    }  else if (input == "wave"){
        motion.wave();
    } else {
        Sprintln(PROGMEM "Unknown command. Type 'help' for a list of commands.");
    }
  }

void handleKeyCommand(char key) {
    switch(key) {
      case 'q': 
        current->setAngle(current->pinC, motion.currAngles[current->index][Coxa] + offsetAngle);
        motion.currAngles[current->index][Coxa]= motion.currAngles[current->index][Coxa] + offsetAngle;
        break;
      case 'a': 
        current->setAngle(current->pinC, motion.currAngles[current->index][Coxa] - offsetAngle); 
        motion.currAngles[current->index][Coxa]= motion.currAngles[current->index][Coxa] -offsetAngle;
        break;
      case 'w': 
        current->setAngle(current->pinF, motion.currAngles[current->index][Femur] + offsetAngle); 
        motion.currAngles[current->index][Femur]= motion.currAngles[current->index][Femur] + offsetAngle;
        break;
      case 's': 
        current->setAngle(current->pinF, motion.currAngles[current->index][Femur] - offsetAngle); 
        motion.currAngles[current->index][Femur]= motion.currAngles[current->index][Femur] - offsetAngle;
        break;
      case 'e': 
        if (current->pinT >= 0 && current->pinT <= 15) { // these tibia servos are on the 16 pin multiplexer
            current->setAngle(current->pinT, motion.currAngles[current->index][Tibia] +offsetAngle); 
        } else {
            current->setAngle(current->pinT, motion.currAngles[current->index][Tibia] +offsetAngle, current->index); 
        }
        motion.currAngles[current->index][Tibia]= motion.currAngles[current->index][Tibia] + offsetAngle;
        break;
      case 'd': 
        if (current->pinT >= 0 && current->pinT <= 15) {
            current->setAngle(current->pinT, motion.currAngles[current->index][Tibia] -offsetAngle); 
        } else {
            current->setAngle(current->pinT, motion.currAngles[current->index][Tibia] -offsetAngle, current->index); 
        }
        motion.currAngles[current->index][Tibia]= motion.currAngles[current->index][Tibia] -offsetAngle ;
        break;
    }
    Sprint(current->name.c_str());
    Sprint(" - Coxa:");
    char temp[5] = {0};
    itoa(motion.currAngles[current->index][Coxa], temp, 10);
    Sprint(temp);
    Sprint("°, Femur:");
    itoa(motion.currAngles[current->index][Femur], temp, 10); // itoa creates null-terminated string so no need to clean
    Sprint(temp);
    Sprint("°, Tibia:");
    itoa(motion.currAngles[current->index][Tibia], temp, 10);
    Sprint(temp);
    Sprintln("°");
}


void printHelp() {
    Sprintln(PROGMEM "\nServo Control System:");
    Sprintln(PROGMEM "Quick commands (single key):");
    Sprintln(PROGMEM "Q/A - Coxa +/-");
    Sprintln(PROGMEM "W/S - Femur +/-");
    Sprintln(PROGMEM "E/D - Tibia +/-");
    Sprintln(PROGMEM "\nAdvanced commands:");
    Sprintln(PROGMEM "stand - Beetlebot in stand position [not a smooth movement]");
    Sprintln(PROGMEM "sit - Beetlebot in sit position [not a smooth movement]");
    Sprintln(PROGMEM "stand up - Beetlebot from sit to stand");
    Sprintln(PROGMEM "sit down - Beetlebot from stand to sit");
    Sprintln(PROGMEM "forward - tripod");
    Sprintln(PROGMEM "rot cw - clockwise tripod gait rotation");
    Sprintln(PROGMEM "rot ccw - counterclockwise tripod gait rotation");
    Sprintln(PROGMEM "forw cw - forward curve clockwise tripod gait");
    Sprintln(PROGMEM "forw ccw - forward curve counterclockwise tripod gait");
    Sprintln(PROGMEM "back cw - backward curve clockwise tripod gait");
    Sprintln(PROGMEM "back ccw - backward curve counterclockwise tripod gait");
    Sprintln(PROGMEM "side left - sideways tripod gait to the left");
    Sprintln(PROGMEM "side right - sideways tripod gait to the right");
}

void Sprintln(const char* msg) {
    if (WEB_SERIAL) {
        ws.printfAll(msg);
    } else {
        Serial.println(msg);
    }
}

void Sprint(const char* msg) {
    if (WEB_SERIAL) {
        ws.printfAll(msg);
    } else {
        Serial.print(msg);
    }
    
}

void sendJson() {
    String temp = String(R"({"act":")") + String(lastInput) +
        String(R"(", "movement_type":)") + String(movementType) + 
        String(R"(, "sensorDe":)") + String(sensorDetect) + 
        String(R"(, "dist0":)") + String(lastDists[0]) + 
        String(R"(, "dist1":)") + String(lastDists[1]) + 
        String(R"(, "dist2":)") + String(lastDists[2]) +  String(R"(})");
    ws.printfAll(temp.c_str());
}

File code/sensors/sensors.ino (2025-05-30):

// The initial code has been taken from the Pololu example that uses multiple sensors.
// The original file is available at https://github.com/pololu/vl53l1x-arduino/blob/master/examples/ContinuousMultipleSensors/ContinuousMultipleSensors.ino

#include "Wire.h"
#include "VL53L1X.h"

const uint8_t sensorCount = 3;

// The Arduino pin connected to the XSHUT pin of each sensor.
// TODO: PINS USED ON THE ARDUINO FOR NOW, WILL NEED TO BE RECHECKED IF THEY'RE AVAILABLE ON THE ESP32
const uint8_t xshutPins[sensorCount] = { 4, 5, 6 };

VL53L1X sensors[sensorCount];

// .ino setup for the wiring and sensors
// TODO: see if wire setup is the same on the ESP32
void setup() {
  while (!Serial) {}
  Serial.begin(115200);
  Wire.begin();
  Wire.setClock(400000); // use 400 kHz I2C

  forceSetup();
}

// try to initiate the sensors until all are good
void forceSetup() {
  while (!trySetup()) {};
}

// Try to setup the sensors, return true iff all are good
bool trySetup() {
  // Disable/reset all sensors by driving their XSHUT pins low.
  for (uint8_t i = 0; i < sensorCount; i++) {
    pinMode(xshutPins[i], OUTPUT);
    digitalWrite(xshutPins[i], LOW);
  }

  // Enable, initialize, and start each sensor, one by one.
  for (uint8_t i = 0; i < sensorCount; i++) {
    // Stop driving this sensor's XSHUT low. This should allow the carrier
    // board to pull it high. (We do NOT want to drive XSHUT high since it is
    // not level shifted.) Then wait a bit for the sensor to start up.
    pinMode(xshutPins[i], INPUT);
    delay(10);

    sensors[i].setTimeout(500);
    if (!sensors[i].init()) return false;

    // Each sensor must have its address changed to a unique value other than
    // the default of 0x29 (except for the last one, which could be left at
    // the default). To make it simple, we'll just count up from 0x2A.
    sensors[i].setAddress(0x2A + i);
    // We decided on Short distance mode since its the least variable and should still be big enough (1.3m no matter the conditions)
    sensors[i].setDistanceMode(VL53L1X::Short);
    sensors[i].setMeasurementTimingBudget(20000); // Minimum for short distance mode (in microseconds)
    sensors[i].startContinuous(20); // Minimum since it must be >= to timing budget (in ms)

  }
    return true;
}

// Check once if sensor i has a new value in mm (non blocking)
// -1 <=> Any error status from .ranging_data.range_status
// -2 <=> New data wasn't available
int checkSensor(int i) {
  //read(false) is non blocking but reading with no data ready has undefined behavior
  if (sensors[i].dataReady()) {
      sensors[i].read(false);
      if (sensors[i].ranging_data.range_status == VL53L1X::RangeValid) {
        return sensors[i].ranging_data.range_mm;
      } else {
        return -1;
      }
    } else {
      return -2;
    }
}

// Get a new value from sensor i in mm (blocking call)
int getFromSensor(int i) {
  int val;
  do {
    val = checkSensor(i);
  } while(val < 0);

  return val;
}

// Simple getter
VL53L1X getSensor(int i) {
  return sensors[i];
}

// Adapted from the example, used for testing on Arduino
void loop() {
  for (uint8_t i = 0; i < sensorCount; i++)
  {
    int val = checkSensor(i);
    if (val>=0) {
      Serial.print(val);
    } else if (val == -1) {
      Serial.print("Error");
    } else {
      Serial.print("Not ready");
    }
    Serial.print('\t');
  }
  Serial.println();
  delay(500);
}

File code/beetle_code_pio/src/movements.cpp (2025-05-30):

#include "data.h"
#include "leg.h"
#include "movements.h"

//no interpolation done - use as set up function
void movements::initializeAllServos(float angleC, float angleF, float angleT) {
    for(uint8_t i = 0; i < 6; i++) {
        legs[i]->setAngle(servoPins[i][Coxa], angleC);
        legs[i]->setAngle(servoPins[i][Femur], angleF);
        if (i == 0) legs[i]->setAngle(servoPins[i][Tibia], angleT, 0);
        else if (i == 1) legs[i]->setAngle(servoPins[i][Tibia], angleT, 1);
        else legs[i]->setAngle(servoPins[i][Tibia], angleT);

        currAngles[i][Coxa] = angleC;
        currAngles[i][Femur] = angleF;
        currAngles[i][Tibia] = angleT;
    }
    delay(SWEEP_DELAY); 
}

void movements::standUp() {

    //as a safe check : should already be at this position
    initializeAllServos(sitAngle[Coxa], sitAngle[Femur], sitAngle[Tibia]);

    int stand1[6][3] = {
        {midStand[Coxa], midStand[Femur], midStand[Tibia]},
        {midStand[Coxa], midStand[Femur], midStand[Tibia]},
        {midStand[Coxa], midStand[Femur], midStand[Tibia]},
        {midStand[Coxa], midStand[Femur], midStand[Tibia]},
        {midStand[Coxa], midStand[Femur], midStand[Tibia]},
        {midStand[Coxa], midStand[Femur], midStand[Tibia]}
    };

    int stand2[6][3] = {
        {standAngle[Coxa], standAngle[Femur], standAngle[Tibia]},
        {standAngle[Coxa], standAngle[Femur], standAngle[Tibia]},
        {standAngle[Coxa], standAngle[Femur], standAngle[Tibia]},
        {standAngle[Coxa], standAngle[Femur], standAngle[Tibia]},
        {standAngle[Coxa], standAngle[Femur], standAngle[Tibia]},
        {standAngle[Coxa], standAngle[Femur], standAngle[Tibia]}
    };

    interpolateAngle(legs, stand1, stepCounter);
    interpolateAngle(legs, stand2, stepCounter);

    //check that every leg is where it needs to be:
    int lift [6][3];
    int angleLift[3] = {90, 70, 125};
    for (int i = 0; i < 6; ++i) {
        angleTabStand(lift, i, angleLift);
        interpolateAngle(legs, lift, stepCounter);
    }

    interpolateAngle(legs, stand2, stepCounter);

}

void movements::angleTabStand (int angles[6][3], int leg, int angleLift [3]) {
    for (int i = 0; i<6; ++i) {
        if (leg == i) {
            angles[leg][0] = angleLift[0];
            angles[leg][1] = angleLift[1];
            angles[leg][2] = angleLift[2];
        } else {
            angles[i][0] = standAngle[0];
            angles[i][1] = standAngle[1];
            angles[i][2] = standAngle[2];
        }
    }
}

void movements::sitDown() {

    initializeAllServos(standAngle[Coxa], standAngle[Femur], standAngle[Tibia]);

    int sit1[6][3] = {
        {midStand[Coxa], midStand[Femur], midStand[Tibia]},
        {midStand[Coxa], midStand[Femur], midStand[Tibia]},
        {midStand[Coxa], midStand[Femur], midStand[Tibia]},
        {midStand[Coxa], midStand[Femur], midStand[Tibia]},
        {midStand[Coxa], midStand[Femur], midStand[Tibia]},
        {midStand[Coxa], midStand[Femur], midStand[Tibia]}
    };

    int sit2[6][3] = {
        {sitAngle[Coxa], sitAngle[Femur], sitAngle[Tibia]},
        {sitAngle[Coxa], sitAngle[Femur], sitAngle[Tibia]},
        {sitAngle[Coxa], sitAngle[Femur], sitAngle[Tibia]},
        {sitAngle[Coxa], sitAngle[Femur], sitAngle[Tibia]},
        {sitAngle[Coxa], sitAngle[Femur], sitAngle[Tibia]},
        {sitAngle[Coxa], sitAngle[Femur], sitAngle[Tibia]}
    };

    interpolateAngle(legs, sit1, stepCounter);
    interpolateAngle(legs, sit2, stepCounter);
}

//helper for a tripod gait
void movements::angleTab2 (int angles[6][3], int walk, int group2 [4][3], int group1 [4][3]) {
    for (int j =0; j<3; ++j) {
        if (j == Coxa) {
            angles[0][j] = group1[walk][j]; // lf
            angles[1][j] = 180 - group2[walk][j]; // rf
            angles[2][j] = group2[walk][j]; // lm
            angles[3][j] = 180 - group1[walk][j]; // rm
            angles[4][j] = group1[walk][j]; //lb
            angles[5][j] = 180 - group2[walk][j]; //rb
        } else {
            angles[0][j] = group1[walk][j]; // lf
            angles[1][j] = group2[walk][j]; // rf
            angles[2][j] = group2[walk][j]; // lm
            angles[3][j] = group1[walk][j]; // rm
            angles[4][j] = group1[walk][j]; // lb
            angles[5][j] = group2[walk][j]; // rb
        }
    }
}

//middle legs have less range of coxa movements as front and back, so needs to rotate less
void movements::angleTab4(int angles[6][3], int walk, int group1 [4][3], int group2[4][3], 
            int middleGroup1 [4][3], int middleGroup2 [4][3]) {
        for (int j =0; j<3; ++j) {
            if (j == Coxa) {
                angles[0][j] = group1[walk][j]; // lf
                angles[1][j] = group2[walk][j]; // rf
                angles[2][j] = middleGroup2[walk][j]; // lm
                angles[3][j] = middleGroup1[walk][j]; // rm
                angles[4][j] = group1[walk][j]; //lb
                angles[5][j] = group2[walk][j]; //rb
            } else {
                angles[0][j] = group1[walk][j]; // lf
                angles[1][j] = group2[walk][j]; // rf
                angles[2][j] = middleGroup2[walk][j]; // lm
                angles[3][j] = middleGroup1[walk][j]; // rm
                angles[4][j] = group1[walk][j]; // lb
                angles[5][j] = group2[walk][j]; // rb
            }
        }  
    }
    

void movements::angleTabSide(int angles[6][3], int walk, int group1 [8][3], int group2[8][3], 
            int middleGroup1 [8][3], int middleGroup2 [8][3]) {
        for (int j = 0; j < 3; ++j) {
            if (j == Coxa) {
                angles[0][j] = group1[walk][j]; // lf
                angles[1][j] = 180 - group2[walk][j]; // rf
                angles[2][j] = middleGroup2[walk][j]; // lm
                angles[3][j] = middleGroup1[walk][j]; // rm
                angles[4][j] = 180 - group1[walk][j]; //lb
                angles[5][j] = group2[walk][j]; //rb
            } else {
                angles[0][j] = group1[walk][j]; // lf
                angles[1][j] = group2[walk][j]; // rf
                angles[2][j] = middleGroup2[walk][j]; // lm
                angles[3][j] = middleGroup1[walk][j]; // rm
                angles[4][j] = group1[walk][j]; // lb
                angles[5][j] = group2[walk][j]; // rb
            }
        }  
    }
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

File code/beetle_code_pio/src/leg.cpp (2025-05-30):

#include "leg.h"

void leg::setAngle(int servoPin, float angle, int servoOnEsp) {
    //pins on the multiplexer
    int offset = servoPin == (pinC) ? offsetCoxa : (servoPin == (pinF) ? offsetFemur : offsetTibia);
    angle = constrain(angle + offset, 0, 180);
    if (servoPin<16) {
        int pulse = angleToPulse(angle);
        multiplexer.setPWM(servoPin, 0, pulse);
    } else {
        uint32_t pulse = map(angle, 0, 180, 500, 2500);
        uint32_t duty = (uint32_t)(pulse * 65536.0 / 20000.0);
        ledcWrite(servoOnEsp, duty);
    }; 
}


int leg::angleToPulse (int pwmAngle) {

    return map(pwmAngle, 0, 180, 125, 625);
}

//maps x from domain in: [min, max] to the corresponding domain out: [min, max]
float mapF(float x, float in_min, float in_max, float out_min, float out_max) {
    return ((x - in_min) * (out_max - out_min) / (in_max - in_min)) + out_min;
}

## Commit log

2025-03-19 added: the material list version 1
2025-03-20 Added: Inverse Kinematics (IK) documentation
2025-04-07 Delete Documentation/Material_bill.md
    This material bill isn't accurate anymore, the current one will be pushed later within the proposal document
2025-04-10 Add: First version of beetlebot's code, can perform basic movements with 3 servos of one leg and a wave movement
2025-04-11 Add files via upload
    Fritzing showing the wiring diagram of the bot
    [BeetleBot_Wiring.fzz]
2025-04-14 Fixed: code so that it works for 18 servos, and added a header file for better readability and modularity.
    [beetle_hdr.h]
2025-04-14 Added to the repo the 3D files so we can start doing PR requests on them
    [BeetleBot.f3d, Chaussette.f3d, Full Leg.f3z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]
2025-04-26 Replaced beetle_code with beetle_code_pio for improved structure and PlatformIO support
    [beetle_hdr.h, main.cpp]
2025-04-29 Added: header file for main and non-working IK gait
    Cleaned up the code by using a header file for main that contains define constants and function prototypes. Added a non-functional implementation of a tripod gait pattern and IK calculations to be re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
2025-05-13 Added .ino file using multiple sensors
    It was written by adapting an example from the library used. It will be converted in the future into .h and .c files for easy inclusions in the main part of the code.
2025-05-15 converted .ino sensors file to .h and .cpp
2025-05-15 Added : non-functional tripod gait implementation
    IsReachable within the leg.cpp needs to be reworked on as now, most of the points we compute, this function decides them unreachable which is an issue as it causes the robot to just not move.
    [data.h, leg.cpp, main.cpp]
2025-05-15 Changed to move the 6 legs at once in main
    Instead of moving by groups of 3, i changed the interpolateAngle to move all of the servos together
2025-05-15 Fixed an issue in the stupid walk
    [main.cpp]
2025-05-15 Fixed the tripod gait 'cycles'
    The cycles that we go through in a loop weren't correct
    [data.h, leg.cpp, main.cpp]
2025-05-19 Fix: first working version of forward stupid walk. Some details need to be reviewed for more stability
    [data.h, main.cpp]
2025-05-25 Added Asyncwebsocket
    The bot can now fully converse via the socket. Input instructions are present on the .html file. SPIFFS need to be loaded for it to work, check the git issue if unsure in how to do so.
    [main.cpp]
2025-05-26 Added a function that goes from sit to stand position + added offsets on the servos that needed them
2025-05-26 Added ability to reconnect to multiplexer if power is lost and restored while the esp32 is on
2025-05-26 Fixed error in offset handling
    [data.h, main.cpp, movements.cpp]
2025-05-26 Fixed offset (other error)
    [main.cpp]
2025-05-27 added the turn + forward functions (not tested) and added the changes to the main accordingly, with added fixes
    [main.cpp, movements.cpp]
2025-05-28 Added angles for right sideways gait, if correct then the mirrored calculations must be done for the left
    [movements.cpp]
2025-05-28 Added the testing bit in the loop and setup to have parrallel communication for the sensors and the servo multiplexer
2025-05-28 Added a Movement type button to the web app
    Movement type that decides whether the bot rotates on itself to follow the direction set or not
2025-05-29 fixed some code and added a few commands
    [main.cpp, movements.cpp]
2025-05-29 added a sensor detection option on the page, fixed sideways, and sit angles
    [data.h, main.cpp, movements.cpp]
2025-05-29 Multiple changes including : stand up, web page, minor fixes
    Added a text box explaining the different movements types and the keyboard / joysticks associated
    For standing up, changed it so each leg lift one by one to avoid them being too far away from the body (hard to explain the issue but should be at the correct position after that)
    Decreased the steps numbers : test, see if it goes a bit faster
    [data.h, main.cpp, movements.cpp]
2025-05-30 Update README.md
    pls someone had assembly instructions
2025-05-30 Added wave movement for the front right leg
2025-05-30 Picture of our circuit
2025-05-30 small fixes
    added back sensor updates
    fixed block animation
    moved wait to default case
    [main.cpp]
2025-05-30 Added all the final CAD components
    [BeetleBot.f3d, Chaussette.f3d, Joint.f3d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]
2025-05-30 fixed offsets and html issues
    [data.h]
2025-05-30 changing name from "Documentation" into "documentation"
    [BeetleBot_Wiring.fzz]
